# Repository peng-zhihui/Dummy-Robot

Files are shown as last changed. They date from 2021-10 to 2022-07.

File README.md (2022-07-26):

# Dummy-Robot: Super compact smart robotic-arm
> **我的超迷你机械臂机器人项目。**
>
> 视频介绍：[【自制】我造了一台 钢 铁 侠 的 机 械 臂 ！【硬核】](https://www.bilibili.com/video/BV12341117rG)
>
> Video : [I made a DUMMY ROBOTIC ARM from scratch！ - YouTube](https://www.youtube.com/watch?v=F29vrvUwqS4)

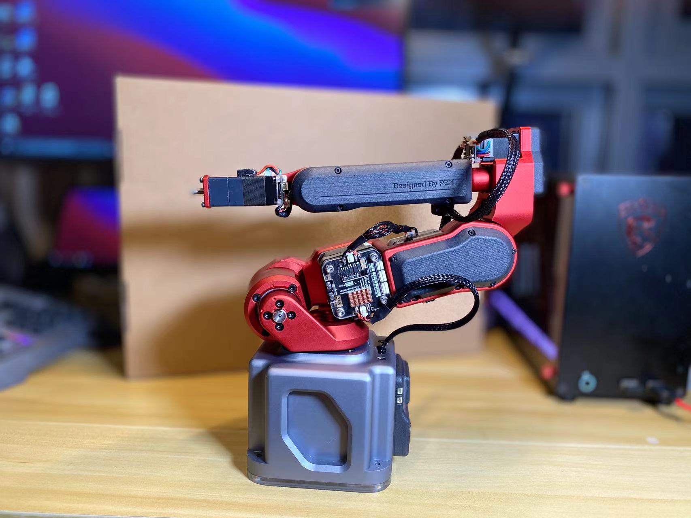
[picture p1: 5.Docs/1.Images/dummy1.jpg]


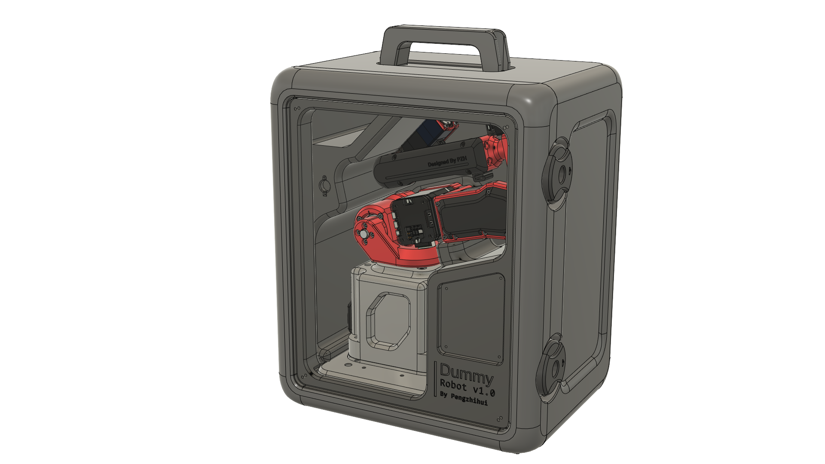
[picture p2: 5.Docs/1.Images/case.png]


### 资料说明（更新日期22-2-9）

* 已添加3D模型设计源文件。
* 已添加夹爪硬件设计文件和LED灯环PCB
* 已添加无线空间定位控制器PCB文件
* 已添加无线示教器Peak软硬件工程（作为submodule）
* 已添加REF的硬件设计文件
* 已添加DummyStudio上位机
* 已添加Dummy核心控制器的固件源代码（使用说明见后文）
* 已添加42步进电机驱动器硬件工程
* 已添加20步进电机驱动器硬件工程
* 已添加42/20步进电机驱动的固件源代码
* 已添加命令行调试工具reftool（基于odrivetool框架）
* 已添加便携手提箱的模型文件

> 这是视频中原版机械臂的完整设计方案，该方案成本和制作难度都比较高，因此想复现的同学建议再等等我后面会发布的**Dummy青春版**，该版本会有如下改进：
>
> 1. 整机重新设计结构，改用3D打印作为制造方案（原版为铝CNC），大幅降低制造成本
> 2. 采用我自己设计的小型摆线针轮减速器替代原版的谐波减速器，大幅降低零件成本
> 3. 所有软件和固件和原版通用，功能也完全一致
> 4. 添加我自己设计的PC端上位机和手机端APP（争取把用户初始化设置引导加进去）
> 5. 改进原版电机驱动器的走线方式，原版电源走线采用焊接的形式，不便于安装和拆卸，后面的青春版会使用4p接插件（电源+CAN总线）连接
> 6. 整机成本争取做到2000以内
> 7. **最重要的，会找人出一个保姆级的视频教程！**

## 关于结构设计

我视频中原版设计使用的`步进电机`+Harmonic的`谐波减速模组`，其中后者成本较高（我买的二手大概是600元一个），因此为了能让大家尽量复现本项目，我后期会添加一个`自制摆线针轮减速器`+`3D打印`的低成本方案。

> 目前摆线减速器已经设计好了正在验证，预期会使用PC（或者亚克力）切割结合3D打印制作，精度有所下降但是功能都保持不变，整机硬件成本希望控制在2000元以内。

设计好的摆线减速器见我的另一个仓库：[peng-zhihui/CycloidAcuratorNano ](https://github.com/peng-zhihui/CycloidAcuratorNano)

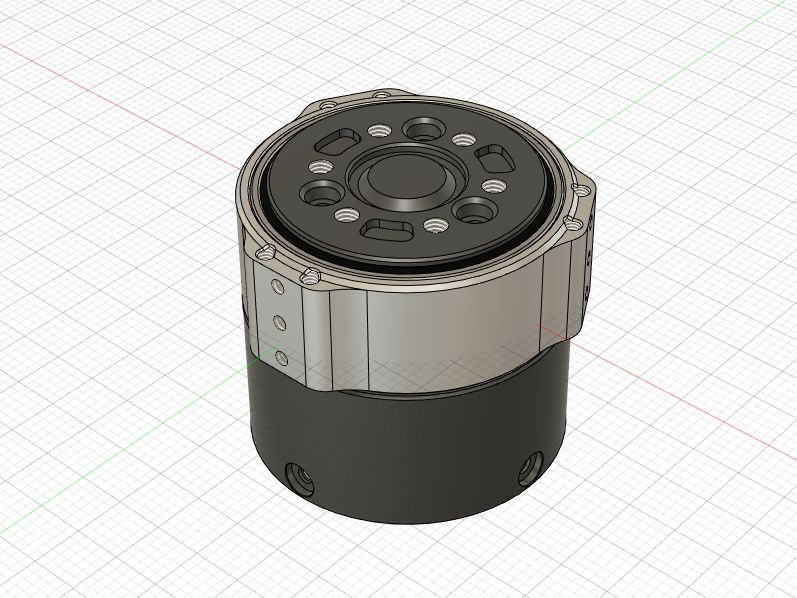
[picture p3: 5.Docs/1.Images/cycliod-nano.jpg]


## 关于电路模块

电路为了实现主要的机械臂运动控制功能其实核心就4块板子：

* REF核心板
* REF底板（也就是机械臂底座里面的控制器电路板）
* 步进电机驱动
* Peak示教器

其中前两者和Peak我都开源了，步进驱动设计的时候参考了： https://github.com/unlir/XDrive 这个项目，这是我一个朋友开源的闭环驱动，基于STM32。该驱动分为开源版和闭源版，闭源版基于分立MOSFET性能极其强劲且功能很完善，开源版用的ADC+斩波驱动芯片，具备基础功能，不带CAN协议。

我重新设计了驱动器的PCB电路（本项目分别用到20、42步进，57的文件只是供大家扩展使用），添加了CAN总线的硬件支持，也对原版核心代码进行了完全重构，**提供编译好的二进制文件可以直接烧录：**

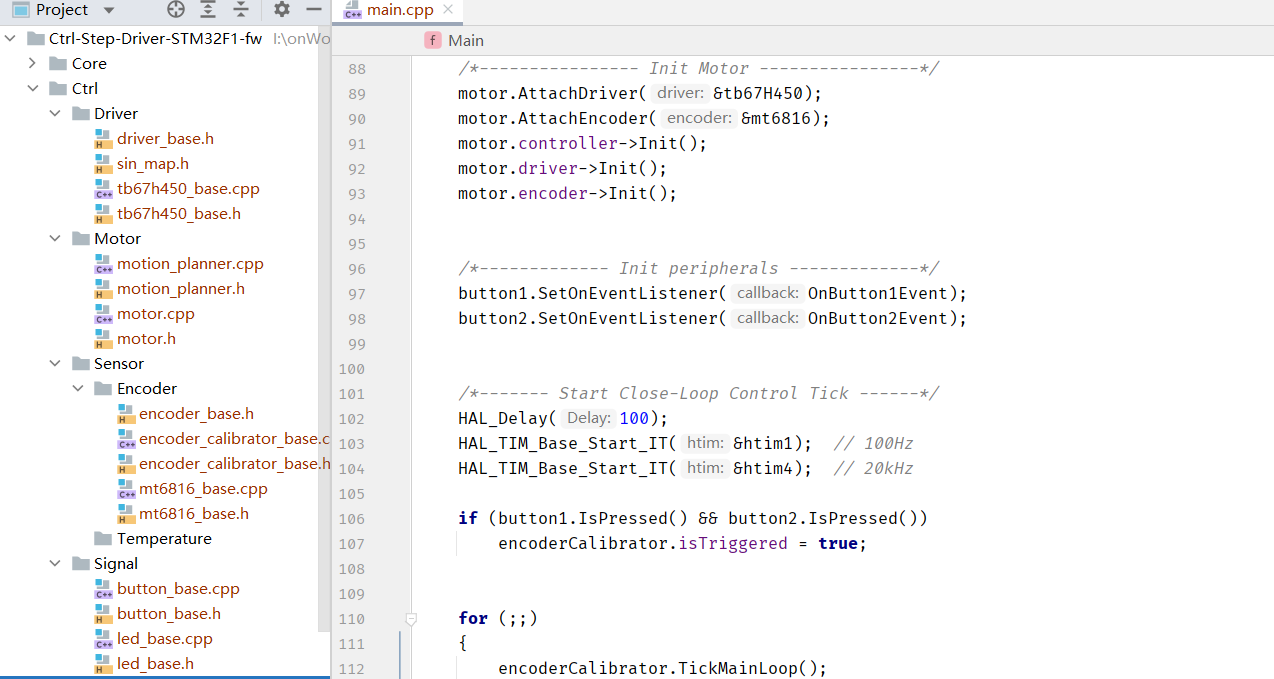
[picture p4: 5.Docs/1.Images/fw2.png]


**主要改进如下：**

1. 使用C++11重构了代码，引入很多高级语言特性，同时底层部分用C混编，不影响代码性能
2. 对硬件依赖完全解耦了，可以方便以后移植到其他平台的MCU，去除了冗余代码代码也结构化逻辑更加清晰
3. 添加了CAN协议和UART协议的自定义模板
4. 添加了模拟EEPROM的参数储存，可以断电保存数据
5. 添加了任意位置设置为零点，且保证双向半圈内归零（而不是单向归零）
6. 完全兼容STM32-HAL库，可以使用STM32CubeMX直接生成配置代码
7. 其他改进，大家二次开发仅需关注UserApp文件夹下的文件即可

Ctrl-Step驱动的使用方式比较简单，下载好固件后，第一次上电电机会进行编码器校准，如果成功则下次上电后按下按键1会进入闭环模式，通过CAN或者串口发送指令即可控制电机，关于指令的说明见源代码`UserApp`文件夹的`interface_can.cpp`和`interface_uart.cpp`：

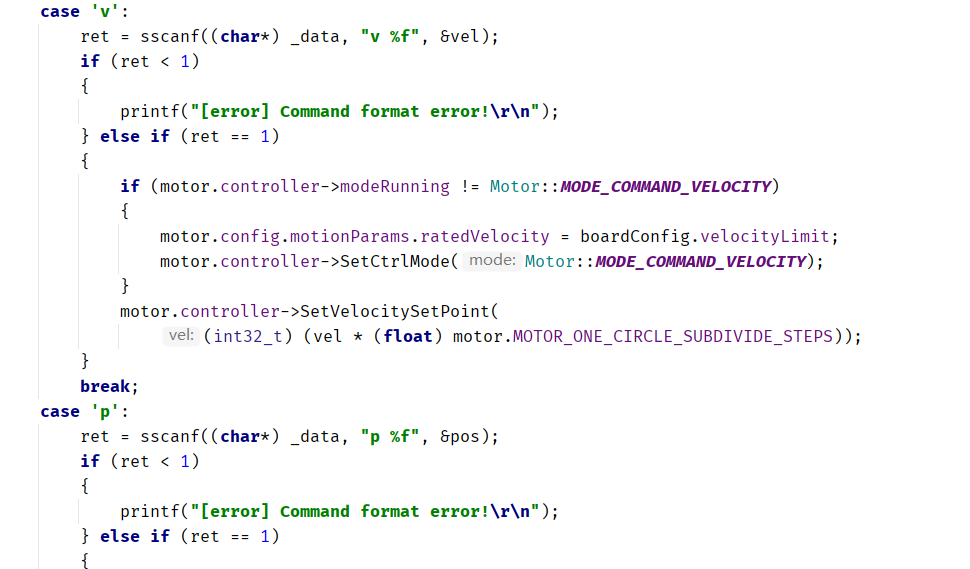
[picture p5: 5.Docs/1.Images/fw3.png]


> 其他按键的作用：
>
> * 同时按住两个按键上电，会自动进行编码器校准，如果首次校准失败可以通过这个方式重新校准
> * 短按按键1在**使能闭环/失能闭环**间切换
> * 长按按键1板子重启
> * 短按按键2清除堵转保护
> * 长按按键2将目标值归零（比如如果是在位置模式那位置会归零）
>
> 其他的功能要通过代码或者通信协议设置，比如设置**home零点**、**PID参数**、CAN节点ID、**各种运动参数**等等，可以自己研究代码。

当然另一种方式是大家也可以自行使用GRBL类的驱动器改装用来驱动本机械臂，这样方案的问题在于，grbl固件耦合性比较强（毕竟不是针对机械臂而是CNC类应用设计的）不便于扩展，另外脉冲形式的控制方式使得走线极其不优雅（每一个关节都要单独拉`step/dir`线到控制器，导致最后几个关节走线很长）。

而我用一体闭环的方式则可以以串联的形式把所有电机连起来即可，走CAN总线使得整体走线只需要四根线（电源正负两根，CAN信号线两根），此外总线模型使得电机可以工作在`力矩`、`速度`、`位置`、`轨迹`模式下，而脉冲模式只能工作在位置和轨迹模式，无法进行复杂控制。

**Peak的话我之前已经软硬件都开源了，可以去SubModules文件夹里面看那边的README说明。**

## 关于核心固件

这个机械臂的固件核心就是运动学姿态解算，~~这块我还在整理，后面会封装得更完善一些进行开源~~，**已开源**，现在写死的很多参数会设计成可配置的，**方便大家用本项目学习完后迁移到自己设计的机械臂中**；同时我把固件从LiteOS框架移植到大家更熟悉的FreeRTOS，方便做二次开发。

**REF的固件使用说明：**

固件主要包括几大功能模块：

* BSP驱动：板载的各种硬件驱动比如OLED、IMU、LED、蜂鸣器、非易失储存等等
* 3rdParty库：包括U8G2的图形库和Fibre的序列化/反序列化库
* Core：ST官方的HAL库
* Driver：ARM的CMSIS驱动
* Midwares：FreeRTOS支持包
* Robot：核心机器人库，包括各种算法和驱动代码
* UserApp：上层应用，可以基于我提供的API接口自行开发其他应用

> * 其中OLED使用Arduino的U8G2库移植而来，可以方便地现实各种调试和系统信息，另外由于STM32的硬件I2C又BUG这里使用了软件I2C驱动屏幕，实测帧率比硬件I2C更高。

`DummyRobot`类是Dummy的完整定义所在，初始化的时候需要设置好**步进电机驱动的信息**以及**自身的DH参数**：

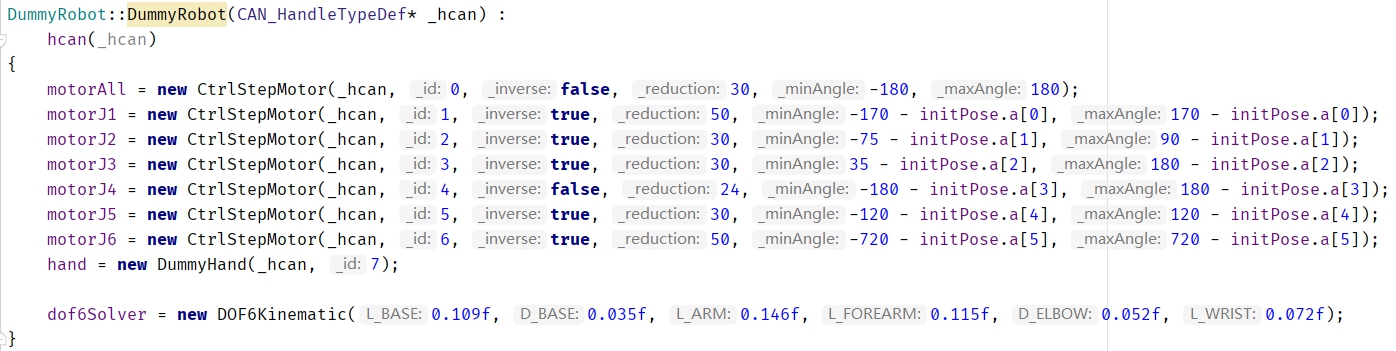
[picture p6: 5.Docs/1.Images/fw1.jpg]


其中驱动器信息包含：CAN节点ID、**是否反向**、减速器的减速比、**运动限制范围**。

而DH参数的含义如下：

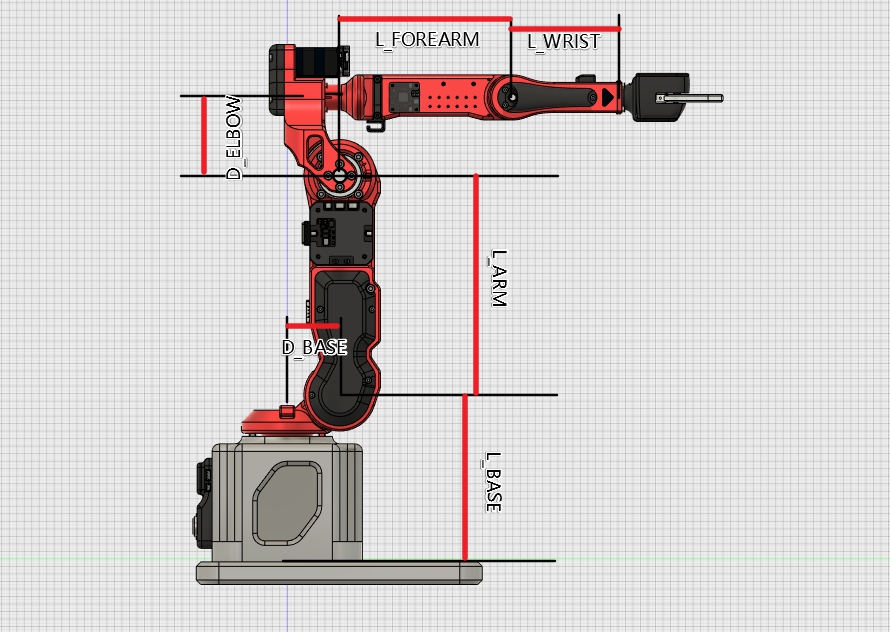
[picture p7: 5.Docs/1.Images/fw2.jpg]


机械臂的构型需要满足Pieper判据（机器人的三个相邻关节轴交于一点或三轴线平行），才能得出解析解，所以大家可以根据Dummy的结构进行修改，然后自己替换DH参数即可以移植我的代码。

> 关于位置的记忆，和上电零点校准：
>
> **由于绝对值编码器的位置只在一圈内有效，工业机械臂经过减速后为了获取绝对位置一般是做输出端编码，但是这样精度就降低了30倍（减速比），所以更合理的是做`双编码器`或者低`功耗编码器+电池`；而我这个项目中双编码器影响结构紧凑设计，所以用了更巧妙的方式：利用电机驱动的电流环控制上电后进行低力矩的无零点定向运动，碰到机械臂限位之后确认粗零点（无限位开关归零），然后根据单圈绝对值编码器的位置精调零点。这个方式的零点是没有误差的，而且几乎不受加工精度影响，因为在12度（360/30）内都是绝对值编码器的有效精度范围。**

**Peak的固件说明：**

Peak基于X-Track项目，大家可以去Peak仓库查看。

## 关于上位机

视频中的软件仿真基于RoboDK，我在视频中开发了连接Dummy的Driver（驱动部分官方document有介绍的，原版是基于TCP网络接口，我修改成了串口并兼容dummy的协议）。不过由于这个软件是收费的，因此我也基于Unity3D开发了自己的上位机，已经发布在仓库。

上位机目前暂时没有计划开源，因为还有很多功能要添加，我也是希望最后能做成一个类似RoboDK的通用软件，大家以后自己做机械臂也能用上，当然软件肯定会是免费的。

## 关于控制算法

首先运动学部分是已经实现了的，正逆解都是传统DH参数计算的，正解（关节角求末端位姿）是唯一解比较好办，逆解（末端位姿求关节角）的话会涉及多解（一般是8个），我这里使用的算法是**求解上一姿态和目标姿态中6个关节变化最大角里面最小的那一组作为逆解采用的config**。这样可以保证机械臂始终以最小转角进行姿态切换。

然后关节角到电机驱动器输入信号的转换这一块，我使用的是梯形加减速曲线进行速度位置规划。举个例子在MoveJ指令中，当收到一个关节角运动指令，控制器会进行运动角度差分计算，得到6个运动差分角度，然后取6个差分角中最大的角θ，同时根据设置的JointSpeed参数计算运动θ角需要的时间（考虑上加减速），把这一时间作为其余5个电机的运动参数计算各自的加减速度&最高速度，然后6个电机根据计算的参数同步运动，就可以保证其同步性和流畅性了。

另外六个电机使用CAN总线连接，每个电机接受两个ID号的信息（自己的ID、0号ID），0号ID作为信息广播和同步用。电机接收到运动指令后将信息储存在影子寄存器中，待收到广播的同步信号后开始运动，这样能进一步保证电机同步性。

最后，动力学部分还在开发中，这块暂时没有完全实现。上**述的运动学和动力学算法都强烈建议去看一下《机器人学导论》这本书**，里面写得非常详细。

## 指令模式

Dummy固件支持三种不同的指令模式（指令可以由USB、串口、CAN接收），不同模式的特性有所区别，见下表：

| | 指令发送频率 | 指令执行方式 | 可被新指令打断 | 指令间停顿 | 适合场景 |
| --- | --- | --- | --- | --- | --- |
| SEQ（顺序指令） | 随机，低（<5Hz）  | FIFO队列依次执行 | 否 | 有 | 一次性发送几个关键点位姿，等待依次执行，可以确保关键点到达；但是由于关键点之间存在减速到0的过程所以存在一定停顿；适合场景例如**视觉抓取、码垛等应用**。 |
| INT（实时指令） | 随机，频率不限 | 指令覆盖，立即执行 | 是 | 无 | 用于实时控制，新指令会覆盖正在执行的指令得到立即响应；但是如果一次性发送一系列指令的话则效果会是只执行最后一条；适合场景例如**动作同步**。 |
| `ToDo`TRJ（轨迹跟踪） | 固定，高（200Hz） | 自动插值，固定周期执行 | 否 | 无 | 适合用于需要进行精确轨迹跟踪的应用，速度会放慢；示例场景比如**3D打印、雕刻、绘画等**。 |

---

> **感谢以下项目作者：**
>
> * [unlir/XDrive: Stepper motor with multi-function interface and closed loop function. 具有多功能接口和闭环功能的步进电机。 (github.com)](https://github.com/unlir/XDrive)
> * [odriverobotics/ODrive: High performance motor control (github.com)](https://github.com/odriverobotics/ODrive)
> * [olikraus/u8g2: U8glib library for monochrome displays, version 2 (github.com)](https://github.com/olikraus/u8g2)
> * [samuelsadok/fibre: Abstraction layer for painlessly building object oriented distributed systems that just work (github.com)](https://github.com/samuelsadok/fibre)

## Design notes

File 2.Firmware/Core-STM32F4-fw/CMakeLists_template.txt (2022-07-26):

#THIS FILE IS AUTO GENERATED FROM THE TEMPLATE! DO NOT CHANGE!
set(CMAKE_SYSTEM_NAME Generic)
set(CMAKE_SYSTEM_VERSION 1)
cmake_minimum_required(VERSION 3.19)

# specify cross compilers and tools
set(CMAKE_C_COMPILER arm-none-eabi-gcc)
set(CMAKE_CXX_COMPILER arm-none-eabi-g++)
set(CMAKE_ASM_COMPILER arm-none-eabi-gcc)
set(CMAKE_AR arm-none-eabi-ar)
set(CMAKE_OBJCOPY arm-none-eabi-objcopy)
set(CMAKE_OBJDUMP arm-none-eabi-objdump)
set(SIZE arm-none-eabi-size)
set(CMAKE_TRY_COMPILE_TARGET_TYPE STATIC_LIBRARY)

# project settings
project(Core-STM32F4-fw C CXX ASM)
set(CMAKE_CXX_STANDARD 17)
set(CMAKE_C_STANDARD 11)

# for use printf & scanf with float
set(COMMON_FLAGS "-specs=nosys.specs -specs=nano.specs -u _printf_float -u _scanf_float")

#Uncomment for hardware floating point
add_compile_definitions(ARM_MATH_CM4;ARM_MATH_MATRIX_CHECK;ARM_MATH_ROUNDING)
add_compile_options(-mfloat-abi=hard -mfpu=fpv4-sp-d16)
add_link_options(-mfloat-abi=hard -mfpu=fpv4-sp-d16)

#Uncomment for software floating point
#add_compile_options(-mfloat-abi=soft)

add_compile_options(-mcpu=cortex-m4 -mthumb -mthumb-interwork)
add_compile_options(-ffunction-sections -fdata-sections -fno-common -fmessage-length=0)

# uncomment to mitigate c++17 absolute addresses warnings
#set(CMAKE_CXX_FLAGS "${CMAKE_CXX_FLAGS} -Wno-register")

if ("${CMAKE_BUILD_TYPE}" STREQUAL "Release")
    message(STATUS "Maximum optimization for speed")
    add_compile_options(-Ofast)
elseif ("${CMAKE_BUILD_TYPE}" STREQUAL "RelWithDebInfo")
    message(STATUS "Maximum optimization for speed, debug info included")
    add_compile_options(-Ofast -g)
elseif ("${CMAKE_BUILD_TYPE}" STREQUAL "MinSizeRel")
    message(STATUS "Maximum optimization for size")
    add_compile_options(-Os)
else ()
    message(STATUS "Minimal optimization, debug info included")
    add_compile_options(-Og -g)
endif ()

include_directories(
        Core/Inc
        Drivers/STM32F4xx_HAL_Driver/Inc
        Drivers/STM32F4xx_HAL_Driver/Inc/Legacy
        Drivers/CMSIS/Device/ST/STM32F4xx/Include
        Drivers/CMSIS/Include
        Middlewares/Third_Party/FreeRTOS/Source/include
        Middlewares/Third_Party/FreeRTOS/Source/CMSIS_RTOS_V2
        Middlewares/Third_Party/FreeRTOS/Source/portable/GCC/ARM_CM4F
        Middlewares/ST/STM32_USB_Device_Library/Core/Inc
        Middlewares/ST/STM32_USB_Device_Library/Class/CDC/Inc
        USB_DEVICE/App
        USB_DEVICE/Target
        3rdParty/fibre/cpp/include
        3rdParty/u8g2
        3rdParty/u8g2/cpp
        Bsp
        Bsp/imu
        Bsp/imu/filters
        Bsp/communication
        Bsp/memory
        Bsp/utils
        Bsp/gpio
        Bsp/utils/software_i2c
        Bsp/utils/arm_math
        Robot
        UserApp
)

add_definitions(-DUSE_HAL_DRIVER -DSTM32F4 -DSTM32F4xx -DSTM32F405xx -DconfigAPPLICATION_ALLOCATED_HEAP)

file(GLOB_RECURSE SOURCES
        "startup/*.*"
        "Drivers/*.*"
        "Core/*.*"
        "UserApp/*.*"
        "3rdParty/*.*"
        "Middlewares/*.*"
        "USB_DEVICE/*.*"
        "Robot/*.*"
        "Bsp/*.*"
        )

set(LINKER_SCRIPT ${CMAKE_SOURCE_DIR}/STM32F405RGTx_FLASH.ld)

add_link_options(-Wl,-gc-sections,--print-memory-usage,-Map=${PROJECT_BINARY_DIR}/${PROJECT_NAME}.map)
add_link_options(-mcpu=cortex-m4 -mthumb -mthumb-interwork)
add_link_options(-T ${LINKER_SCRIPT})

link_directories("Drivers/CMSIS/Lib")
link_libraries("arm_cortexM4lf_math.a")

add_executable(${PROJECT_NAME}.elf ${SOURCES} ${LINKER_SCRIPT})

set(HEX_FILE ${PROJECT_BINARY_DIR}/${PROJECT_NAME}.hex)
set(BIN_FILE ${PROJECT_BINARY_DIR}/${PROJECT_NAME}.bin)

add_custom_command(TARGET ${PROJECT_NAME}.elf POST_BUILD
        COMMAND ${CMAKE_OBJCOPY} -Oihex $<TARGET_FILE:${PROJECT_NAME}.elf> ${HEX_FILE}
        COMMAND ${CMAKE_OBJCOPY} -Obinary $<TARGET_FILE:${PROJECT_NAME}.elf> ${BIN_FILE}
        COMMENT "Building ${HEX_FILE}
Building ${BIN_FILE}")

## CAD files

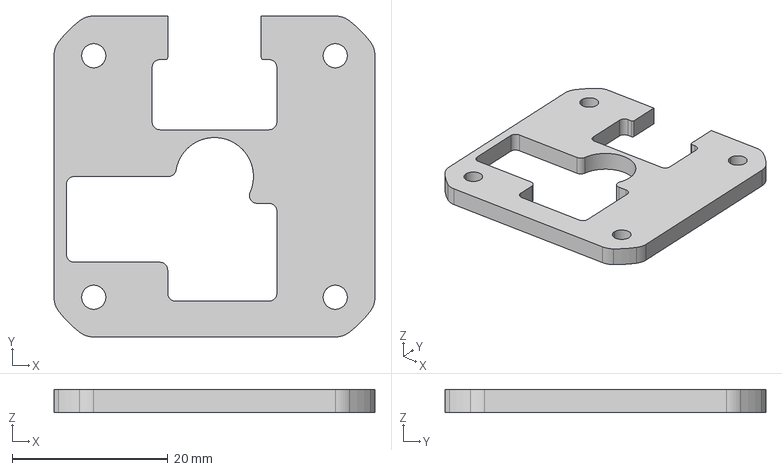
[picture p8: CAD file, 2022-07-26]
4.Model/Motor42-下盖.step
41.2 x 41.2 x 3.00 mm

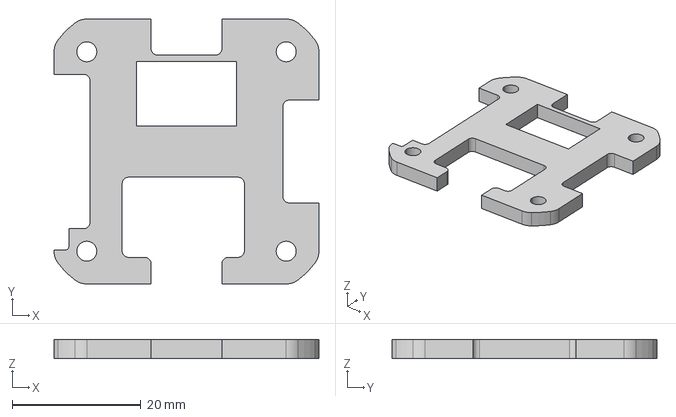
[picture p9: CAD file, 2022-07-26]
4.Model/Motor42-上盖.step
41.2 x 41.2 x 3.00 mm

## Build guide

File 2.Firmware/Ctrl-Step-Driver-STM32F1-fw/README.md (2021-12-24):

使用STM32CubeMX重新生成工程后，需要取消`stm32f1xx_it.c`的更改。

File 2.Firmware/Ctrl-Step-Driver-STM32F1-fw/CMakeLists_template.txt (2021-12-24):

#THIS FILE IS AUTO GENERATED FROM THE TEMPLATE! DO NOT CHANGE!
set(CMAKE_SYSTEM_NAME Generic)
set(CMAKE_SYSTEM_VERSION 1)
cmake_minimum_required(VERSION 3.20)

# specify cross compilers and tools
set(CMAKE_C_COMPILER arm-none-eabi-gcc)
set(CMAKE_CXX_COMPILER arm-none-eabi-g++)
set(CMAKE_ASM_COMPILER arm-none-eabi-gcc)
set(CMAKE_AR arm-none-eabi-ar)
set(CMAKE_OBJCOPY arm-none-eabi-objcopy)
set(CMAKE_OBJDUMP arm-none-eabi-objdump)
set(SIZE arm-none-eabi-size)
set(CMAKE_TRY_COMPILE_TARGET_TYPE STATIC_LIBRARY)

# project settings
project(Ctrl-Step-STM32-fw C CXX ASM)
set(CMAKE_CXX_STANDARD 17)
set(CMAKE_C_STANDARD 11)

#Uncomment for hardware floating point
#add_compile_definitions(ARM_MATH_CM4;ARM_MATH_MATRIX_CHECK;ARM_MATH_ROUNDING)
#add_compile_options(-mfloat-abi=hard -mfpu=fpv4-sp-d16)
#add_link_options(-mfloat-abi=hard -mfpu=fpv4-sp-d16)

#Uncomment for software floating point
#add_compile_options(-mfloat-abi=soft)

add_compile_options(-mcpu=cortex-m3 -mthumb -mthumb-interwork)
add_compile_options(-ffunction-sections -fdata-sections -fno-common -fmessage-length=0)

# uncomment to mitigate c++17 absolute addresses warnings
#set(CMAKE_CXX_FLAGS "${CMAKE_CXX_FLAGS} -Wno-register")

if ("${CMAKE_BUILD_TYPE}" STREQUAL "Release")
    message(STATUS "Maximum optimization for speed")
    add_compile_options(-Ofast)
elseif ("${CMAKE_BUILD_TYPE}" STREQUAL "RelWithDebInfo")
    message(STATUS "Maximum optimization for speed, debug info included")
    add_compile_options(-Ofast -g)
elseif ("${CMAKE_BUILD_TYPE}" STREQUAL "MinSizeRel")
    message(STATUS "Maximum optimization for size")
    add_compile_options(-Os)
else ()
    message(STATUS "Minimal optimization, debug info included")
    add_compile_options(-Og -g)
endif ()

include_directories(
        Core/Inc
        Drivers/STM32F1xx_HAL_Driver/Inc
        Drivers/STM32F1xx_HAL_Driver/Inc/Legacy
        Drivers/CMSIS/Device/ST/STM32F1xx/Include
        Drivers/CMSIS/Include
        Ctrl
        Ctrl/Sensor
        Ctrl/Signal
        Ctrl/LowLevel
        Ctrl/MotorControl
        UserApp
        Port
)

add_definitions(-DUSE_HAL_DRIVER -D__MICROLIB -DSTM32F1 -DSTM32F1xx -DSTM32F103xB)

file(GLOB_RECURSE SOURCES
        "startup/*.*"
        "Drivers/*.*"
        "Core/*.*"
        "Ctrl/*.*"
        "UserApp/*.*"
        "Port/*.*"
        )

set(LINKER_SCRIPT ${CMAKE_SOURCE_DIR}/STM32F103CBTx_FLASH.ld)

add_link_options(-Wl,-gc-sections,--print-memory-usage,-Map=${PROJECT_BINARY_DIR}/${PROJECT_NAME}.map)
add_link_options(-mcpu=cortex-m3 -mthumb -mthumb-interwork)
add_link_options(-T ${LINKER_SCRIPT})

add_executable(${PROJECT_NAME}.elf ${SOURCES} ${LINKER_SCRIPT})

set(HEX_FILE ${PROJECT_BINARY_DIR}/${PROJECT_NAME}.hex)
set(BIN_FILE ${PROJECT_BINARY_DIR}/${PROJECT_NAME}.bin)

add_custom_command(TARGET ${PROJECT_NAME}.elf POST_BUILD
        COMMAND ${CMAKE_OBJCOPY} -Oihex $<TARGET_FILE:${PROJECT_NAME}.elf> ${HEX_FILE}
        COMMAND ${CMAKE_OBJCOPY} -Obinary $<TARGET_FILE:${PROJECT_NAME}.elf> ${BIN_FILE}
        COMMENT "Building ${HEX_FILE}
Building ${BIN_FILE}")

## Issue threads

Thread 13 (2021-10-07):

求双目跟踪定位部分

xuebuaa, 2021-10-07:
红外LED辅助识别是提升定位精度吗？

APeiZou, 2021-10-08:
@peng-zhihui 双目跟踪定位用的什么算法啊

eqio, 2021-10-10:
@peng-zhihui 大神后面有什么简单的活，可以丢给我们练练手^_^。

peng-zhihui, 2021-10-19:
> @peng-zhihui 您好，这个[https://www.zhihu.com/question/36255080/answer/707967657项目的算法有开源吗？](https://www.zhihu.com/question/36255080/answer/707967657%E9%A1%B9%E7%9B%AE%E7%9A%84%E7%AE%97%E6%B3%95%E6%9C%89%E5%BC%80%E6%BA%90%E5%90%97%EF%BC%9F)

这个没有开源，很早以前在学校做的，我这边资料也不全了

fatsheep2020, 2024-02-18:
> 跟我的这个项目用到的技术是一样的： https://www.zhihu.com/question/36255080/answer/707967657
>
> 简单说就是，红外LED的图像经过二值化、轮廓查找得到大概位置，然后形态学处理和卡尔曼滤波得到精确预估位置，再用两个图像中的坐标视差计算Z轴深度得到三维坐标

这个链接不能访问了。。。

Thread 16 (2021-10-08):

请问工业设计 用什么软件，求技术路线，我也想自己学习做一套

weilingwei, 2021-10-08:
请问工业设计 用什么软件，求技术路线，我也想自己学习做一套

LeesCode, 2021-10-08:
法律问题我确实没想到（主要是免费的确实习以为常了，但严格来讲确实有风险）。不过就软件上手容易程度和后续静力动力仿真Solidworks更好一些，萝卜白菜各有所爱，还是看个人习惯。

eqio, 2021-10-08:
> 法律问题我确实没想到（主要是免费的确实习以为常了，但严格来讲确实有风险）。不过就软件上手容易程度和后续静力动力仿真Solidworks更好一些，萝卜白菜各有所爱，还是看个人习惯。

事实上，作者的开源已经算比较彻底了。虽然是通用格式，但大家都可以打开，如果想仔细研究，部分零件可以自己用自己习惯的软件重绘一次，也算加深印象了。

peng-zhihui, 2021-10-10:
我最开始用的Rhinoceros，去年转的Fusion360，f3d的文件别的软件打不开，step是最通用的，而且可以转成各种软件里的格式。

Q-fei, 2021-10-21:
fusion 360 感觉用起来不是很顺手，之前有用过，装配而言有点迷 反正我经常在装配的时候发生模型重叠现象 也不知道是不是我方法用错了，工业模型我用的还是soildworks

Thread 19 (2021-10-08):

同步现实部分能不能加在真正的中小型机械臂上阿

ZXin0305, 2021-10-08:
如题，如果可以的话，希望这一部分能够开源，也能够作为比较好的人机交互方式了，大神太强了！！！！

ballballu, 2021-10-08:
htc 有一个vive tracker。你可以用这个设备和这边的开源代码[vive-tracker](https://github.com/moon-wreckers/vive_tracker)，实现在ros框架下对机械臂的操作。我自己这边是用这个来遥操作ur5、tiago这样的机器人

ZXin0305, 2021-10-09:
> htc 有一个vive tracker。你可以用这个设备和这边的开源代码[vive-tracker](https://github.com/moon-wreckers/vive_tracker)，实现在ros框架下对机械臂的操作。我自己这边是用这个来遥操作ur5、tia

ZXin0305, 2021-10-09:
> htc 有一个vive tracker。你可以用这个设备和这边的开源代码[vive-tracker](https://github.com/moon-wreckers/vive_tracker)，实现在ros框架下对机械臂的操作。我自己这边是用这个来遥操作ur5、tiago这样的机器人

多谢，有时间去试一试

Closed 2021-10-09.

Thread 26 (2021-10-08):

有兴趣开源ps5力反馈扳机的相关代码么

ballballu, 2021-10-08:
今年2月做手持力反馈装置的时候考虑过ps5那个扳机，结果不是很理想。今年看了大佬做的这个，感觉好像很不错

peng-zhihui, 2021-10-10:
PS5手柄的扳机改造是把零件上的所有硬件连接到自己的PCB上控制反馈，相当于换主控，具体可以参考我发的原理图PCB

peng-zhihui, 2021-10-10:
代码开发时间原因其实实现得还很简单，就是几个PID控制环，这种反馈的效果主要受限于硬件，所以用PS5的硬件做效果可以很好

Closed 2021-10-10.

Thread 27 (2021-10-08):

有想要复现的同学一起拼个团吗？

Khala-Yang, 2021-10-08:
CNC金属外壳部分，不知道3D打印的可不可以 >_<

S1aoXuan, 2021-10-09:
准备跟组里的兄弟的复现但是硬件是着实不会>.<

Hconk, 2021-10-09:
建了个群有兴趣复现的可以一起讨论下(纯技术交流及成果分享),  希望可以使用其他的减速电机作为替代品，在尽量降低成本的同时能获得相对较高的精度， 一些物料如果批量做报价应该可以低些。 538103629

captain-zhang, 2021-10-09:
准备复现或者自制的同学可以加我啊，各方面都懂一点，可以团一个出来。QQ 741243893

Khala-Yang, 2021-10-09:
这么贵的吗！... 实属无知者无畏(捂脸)

billhhh, 2021-10-10:
举手，一起啊

xiangxing98, 2021-10-10:
赞一个

Khala-Yang, 2021-10-10:
逛了一圈GIthu，发现了有个便宜一点的 [SmallRobotArm](https://github.com/SkyentificGit/SmallRobotArm)，都是3D打印件，也没有用很贵的电机，预估千元以内，吃吃土还是拿的下的。
稚晖君的这个机械臂Sooo Sexy！但要复刻一个就真得喝西北风了...
我永远相信稚晖君的审美，可我的钱包不相信我>_<！

chenwh14, 2021-10-10:
初步看了一下模型，发现有CSF-8-30，CSF-5-30两种Harmonic的谐波减速器，全新的话不会便宜……二手的话应该也难有靠谱的渠道啊

Hconk, 2021-10-10:
> 初步看了一下模型，发现有CSF-8-30，CSF-5-30两种Harmonic的谐波减速器，全新的话不会便宜……二手的话应该也难有靠谱的渠道啊

从模型里面数了下用的电机。

电机 | 个数
-- | --
PK513PA-H50S | 3
CSF-5-30-1U | 2
CSF-8-30-1U | 2
Nema17 Stepper Motor | 2
CRK543AP-H50 | 1

peng-zhihui, 2021-10-10:
谐波的成本很高，其实我是希望有同学有空修改一下模型改成行星减速方案（其实也不难），然后3D打印机身，精度虽说和我视频中比不了，但是比一般的舵机机械臂是要强很多的，而且后面代码可以通用

SinKy-Yan, 2021-10-10:
其实行星的话感觉可以试试DJI的那两个给比赛做的电机，[M3508](https://www.robomaster.com/zh-CN/products/components/general/M3508)和[M2006](https://www.robomaster.com/zh-CN/products/components/general/M2006) 这两个的回差应该在可接受的范围内，不知道有没有大佬去看看

GitHubHun, 2021-10-11:
我来看看大家在聊什么我看不懂的东西;

Fanjustfan, 2021-10-12:
想要复现+1 大佬们有群吗 交流比较方便

liubog2008, 2021-10-13:
https://join.slack.com/t/just-for-funco/shared_invite/zt-wysbftd3-iguJ4uYk2n9TgtX6fmkx0A 发个 slack 链接，欢迎大家加入

willshion, 2021-10-13:
求行星 复现 1k左右踢我

captain-zhang, 2021-10-15:
> 求行星 复现 1k左右踢我

1K 你还是歇着吧

MuNineyi, 2021-12-14:
> https://join.slack.com/t/just-for-funco/shared_invite/zt-wysbftd3-iguJ4uYk2n9TgtX6fmkx0A 发个 slack 链接，欢迎大家加入

可以给个 slack 的邀请链接么，原连接过期了

fumingxi, 2021-12-20:
我3D打印了一套对应的金属件，强度还可以，不过对PCB之类的不通（纯软件出身）。。有没有大佬篇硬件的一起搞一下。？

StarJi1991, 2022-02-21:
查了一下这个电机价格是认真的？

52chengcheng, 2022-06-28:
有没有群，邀一下

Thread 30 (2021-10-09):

给大佬提个进一步开发建议。供参考。（另：第一次离大佬这么近！激动！！）

sipgov, 2021-10-09:
大佬可以考虑开发各种模块化的合成设备，比如机械臂+AI模块+智能自行系统，则可以化身成为战场上的智能医疗机器人。机械臂+矢量杠杠动力放大模块，就可以成为真正的工业生产机器人。这样将来商业化运作时，客户可以根据自己需求按需购买不同模块组合。

peng-zhihui, 2021-10-10:
我这些都是自己业余DIY项目所以没太考虑商业化哦，不过你说的模块化思路其实我是会做的

TANG-N, 2021-10-14:
有了这只手，加只眼，是不是就能陪打乒乓球了

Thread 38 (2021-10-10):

咨询zhihui兄，从事这些DIY平时的资金投入情况

jpixy, 2021-10-10:
很久之前，几乎是从zhihui君在大学时候作寻线机器人开始，就一直关注zhihui兄的DIY，也深受启发。

我最大的问题是，其实zhihui兄之前也曾透露过花过不少钱，但是一直没有一个具体的数量级。

所以，还是希望zhihui兄能否大概给出个从入门到平时开发的大体的资金投入，个人想得以参考：

1. 原材料的费用，小的电子元器件估计费用不大，但是一些CPU等重要芯片和制作PCB板子，和作废板子等费用应该投入不小(每次小几百，小一千，累积多了也不少费用估计)，能否具体说说？
2. 这个机械臂成品费用一万元左右，但是从开发到设计，debug，作废等考虑进去，总计会投入多少？
3. 由此，针对一般的DIY的开发，资金投入分布大概什么样子呢？比如作废板子大概占6,7成总费用等。能否给出个资金占比？当然详单更好。
4. 除了这些，那些工具一次性的投入，估计还好。不管是焊台，还是3D打印机基本上都是一次性投入，这部分也能出个大概的清单吗？
5. 总而言之，想知道zhihui兄，平时维持这个DIY爱好，资金投入的大体情况，以供参考。

不知道这个是不是敏感话题，之前在给您的个人邮箱pengzhihui.david@foxmail.com 发过邮件咨询类似问题。如果不方便在issue里公开回答，是否可以邮件给我: johnny@jpixy.com一些指导和答复？

谢谢！
Johnny

peng-zhihui, 2021-10-10:
1. 元器件库是持续积累的，比如可以去买一个电阻电容本，型号很全性价比也很高，除了最近出现的芯片涨上天的情况，其余器件有个1、2000元足够囤一堆了
2. 费用主要就是减速器和PCB打样，详细的没算，总之不超过2w吧
3. 上面说了，可以屯一个元件库，根据项目持续补充
4. 我以前报道里说过，我在大学为了买工具和元件做比赛，连饭都吃不起了，而我生活费也才一个月1000当时也做出了很多有意思的东西；所以投入这种事情往上了看就不封顶了，我条件好了之后买工具都是很舍得投入的，但是往下看，只要每月有个几百块也完全足够。

Closed 2021-10-10.

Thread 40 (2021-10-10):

关于位置的记忆，每次上电都需要零点校准吗？

eqio, 2021-10-10:
我的理解是步进的绝对位置是从上电开始计算的。在断电后是否需要归零，6个轴是分别校准的吗？

peng-zhihui, 2021-10-11:
绝对位置只在一圈内有效，经过减速后为了获取绝对位置一般是做输出端编码，但是这样精度就降低了30倍（减速比），所以更合理的是做双编码器，而我这个项目中双编码器影响结构紧凑设计，所以用了更巧妙的方式：利用电机驱动的电流环控制上电后进行低力矩的无零点定向运动，碰到机械臂限位之后确认零点。这个方式的零点是没有误差的，而且几乎不受加工精度影响，因为在12度（360/30）内都是绝对值编码器的有效精度范围。

eqio, 2021-10-11:
@peng-zhihui 小系统而言，您的实现已经很巧妙了。只是实际应用中限位开关好像也是必须的，且不一定每次能去零点校准，也许有工件。商业应用是另一个范畴，个人觉得。

zhbi98, 2025-05-23:
为什么 Dummy 要设置两次零点？第一次是 L 形的时候设置一下，复位姿势后在设置一下。在机械臂回到休息姿势（Resting Pose）后再应用一次“当前位置作为零点”（ApplyPositionAsHome），那么最后零点不就会以休息姿势来定义

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

Closed 2021-10-11.

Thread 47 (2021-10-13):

稚辉君你好，请问robodk部分的驱动会开源出来吗？

JunJie-zhang-o, 2021-10-13:

JunJie-zhang-o, 2021-10-13:
因为之前有修改过部分的离线编程的代码，但是关于驱动部分并没有做太多了解，看您视频中使用的是robodk的驱动，想学习下robodk驱动部分！！！

peng-zhihui, 2021-10-13:
驱动部分官方document有介绍的，原版是基于TCP网络接口，我修改成了串口，另外我自己的上位机已经更新了。

wxfzy, 2021-10-16:
稚晖君，你的上位机会开源吗？

yijiehe-oss, 2021-11-03:
在你的基础上在开发做创新可以吗？

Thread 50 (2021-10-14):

大佬，步进电机驱动好像没有放到文件里

Jzacky, 2021-10-14:

CaoZengxu, 2021-10-14:
大佬已经明确说了这部分不开源。建议写到readme里，防止大🔥还有不必要的期待。

Jzacky, 2021-10-14:
> > 大佬已经明确说了这部分不开源。建议写到readme里，防止大🔥还有不必要的期待。
>
> 没有说这部分不开源啊，是说会出一个简化版的开源。

哦哦，谢谢大佬

Riva34, 2021-10-30:
对呀，连我这个65岁的老骨头都在泰国慢慢学习。所有部件都要用两个星期时间寄到泰国。

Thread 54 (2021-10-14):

偶像能不能把上位机软件的项目代码也开源呀，想要学习学习

nishiwodelian, 2021-10-14:
感谢

HackEFA, 2021-10-14:
[Assembly-CSharp.zip](https://github.com/peng-zhihui/Dummy-Robot/files/7345792/Assembly-CSharp.zip)
SW: dnSpy
需要增加unity引擎引用

nishiwodelian, 2021-10-14:
> [Assembly-CSharp.zip](https://github.com/peng-zhihui/Dummy-Robot/files/7345792/Assembly-CSharp.zip) SW: dnSpy 需要增加unity引擎引用
太感谢了，除了这些脚本文件，完整的unity项目文件您还有吗

HackEFA, 2021-10-14:
那个你download下来dll就行，unity3D软件向导配置就可以加载需要的那部分插件，主要内容在这个C#里面。
可以参考https://www.youtube.com/watch?v=MQKJfZCAEa8
我并没有这个项目的全部工程，要看大佬是否开源了，C#这部分是主要机械臂实现的主要部分和接口。

nishiwodelian ***@***.***> 于2021年10月14日周四 下午8:37写道：

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

Ice-Panda, 2021-10-19:
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

稚晖君你好，我想请教一下Dummy Studio中，网格地板和右上角的坐标轴是如何实现的，为什么可以和编辑模式下几乎一样。

Closed 2021-10-14.

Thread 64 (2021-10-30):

代码注释 全英文的啊？

sampletea, 2021-10-30:

peng-zhihui, 2021-10-30:
是啊，因为很多外国友人也要做

peng-zhihui, 2021-10-30:
是啊，我注释一般习惯写英文，因为中文编码容易出问题，而且很多外国友人也要做

Alansortorz, 2021-10-30:
哈哈  太真实了  CLion哪个写32的程序，中文注释，动不动就成乱码了

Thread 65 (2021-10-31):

实际控制的入口是在哪 我看了这几个线程  就直接dummy.UpdateJointPos(); 里边用can发数据了？

sampletea, 2021-10-31:
CommunicationTask    ThreadOledUpdate   ThreadControlLoop  ？ 实际控制 目标位置 啊    计算姿态啥的 从哪里进去？
  对RTOS不是很懂 ！！！ 勉强看看这三个线程    大佬 指点一下！

peng-zhihui, 2021-11-04:
机械臂是接受上位机指令的，指令解析看protocol里面的代码，最终都是调用MoveJ和MoveL进行姿态解算

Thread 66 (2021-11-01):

咨询一下atlas200的开发套件相关的硬件配置。

wangweiqing, 2021-11-01:
hello，看到动作捕获那部分，使用了双目摄像头加一个atlas200的卡，想咨询一下，那个搭载atlas卡的开发板相关配置是什么？目前有有一些兴趣去做一下这部分相关的东西。

peng-zhihui, 2021-11-04:
https://e.huawei.com/cn/products/cloud-computing-dc/atlas/atlas-200
不过现在已经没有对外提供了，新一代产品明年会出

wangweiqing, 2021-11-04:
淘宝上还有存量的产品~只不过主要是4G的版本，8G版本的会比较少。

Closed 2021-11-04.

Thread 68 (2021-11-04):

DH参数好像不对？是不是我搞错了？D_ELBOW不应该是连杆的长度a吗？为啥是d

guguobao, 2021-11-04:
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

peng-zhihui, 2021-11-04:
你搞错了，D是连杆偏移，L才是长度，注意我模型里面是有角度Offset的，3轴的角度旋转了90度

guguobao, 2021-11-04:
> 你搞错了，D是连杆偏移，L才是长度，注意我模型里面是有角度Offset的，3轴的角度旋转了90度
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
D_ELBOW连杆偏移好像是沿着关节3的Z轴偏移的是吧？
但我看实物D_ELBOW更像是连杆的长度，沿着关节3的x轴偏移。总觉得和实物不太符合？我用的是标准DH建模思路，不知道思路对不对？望大佬指点

guguobao, 2021-11-04:
我猜你的正解并没有使用到DH参数中的d和a，因此你的程序在使用中是没问题的，

guguobao, 2021-11-04:
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
想请教下L1_BASE、L2_ARM、L3_ELBOW、L6_WRIST这四个向量的初始值缘由？

peng-zhihui, 2021-11-04:
当然用了啊，不用怎么正逆解，代码里都有

发自我的iPhone

------------------ 原始邮件 ------------------
发件人: guguobao ***@***.***&gt;
发送时间: 2021年11月4日 13:54
收件人: peng-zhihui/Dummy-Robot ***@***.***&gt;
抄送: 稚晖 ***@***.***&gt;, Comment ***@***.***&gt;
主题: 回复：[peng-zhihui/Dummy-Robot] DH参数好像不对？是不是我搞错了？D_ELBOW不应该是连杆的长度a吗？为啥是d (Issue #68)

peng-zhihui, 2021-11-04:
你把机械臂三轴抬起90度机械臂竖直一条线就会明白了

发自我的iPhone

------------------ 原始邮件 ------------------
发件人: guguobao ***@***.***&gt;
发送时间: 2021年11月4日 13:54
收件人: peng-zhihui/Dummy-Robot ***@***.***&gt;
抄送: 稚晖 ***@***.***&gt;, Comment ***@***.***&gt;
主题: 回复：[peng-zhihui/Dummy-Robot] DH参数好像不对？是不是我搞错了？D_ELBOW不应该是连杆的长度a吗？为啥是d (Issue #68)

peng-zhihui, 2021-11-04:
> 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 想请教下L1_BASE、L2_ARM、L3_ELBOW、L6_WRIST这四个向量的初始值缘由？

坐标系是右手坐标，图中右为X+，上为Z+；那个d/a只是临时变量，没有用到，后面实际直接用DH_matrix里面的变量了

guguobao, 2021-11-04:
好的，我刚刚猜到了L1_BASE、L2_ARM、L3_ELBOW、L6_WRIST的定义的，是不是这样的，比如L1_BASE= {armConfig.D_BASE, -armConfig.L_BASE, 0.0f}，L1_BASE即是把D_BASE看成在R[0]旋转后的坐标系x轴方向的值,  L_BASE看成R[0]旋转后的坐标系y轴方向的值 ,
如图：

guguobao, 2021-11-04:
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

guguobao, 2021-11-04:
望指导，十分感谢

peng-zhihui, 2021-11-04:
> 望指导，十分感谢

是的理解正确，简单讲L都是本身臂长，D是和臂长垂直方向的偏移

peng-zhihui, 2021-11-04:
另外初始角度偏移90°是当时为了和RoboDK里面的参数匹配

guguobao, 2021-11-04:
好的，谢谢了，我还想问问逆解，有什么好的方法理解 关节2有四组解，每组解得几何推导，有点难理解

guguobao, 2021-11-04:
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

peng-zhihui, 2021-11-04:
可以看一下林沛群教授的视频课程，讲得很好

发自我的iPhone

------------------ 原始邮件 ------------------
发件人: guguobao ***@***.***&gt;
发送时间: 2021年11月4日 20:35
收件人: peng-zhihui/Dummy-Robot ***@***.***&gt;
抄送: 稚晖 ***@***.***&gt;, Comment ***@***.***&gt;
主题: 回复：[peng-zhihui/Dummy-Robot] DH参数好像不对？是不是我搞错了？D_ELBOW不应该是连杆的长度a吗？为啥是d (Issue #68)

好的，谢谢了，我还想问问逆解，有什么好的方法理解 关节2有四组解，每组解得几何推导，有点难理解

—
You are receiving this because you commented.
Reply to this email directly, view it on GitHub, or unsubscribe.
Triage notifications on the go with GitHub Mobile for iOS or Android.

guguobao, 2021-11-05:
我又来麻烦你了，林沛群得机器人学我看完逆解部分了，它仅仅提到欧拉角zyz，没有提到已知zyz欧拉矩阵去反推角度。zyz欧拉矩阵（好像就是等同rotz(theta4)*roty(theta5)*rotz(theta6)（右乘，相对旋转），正好对上关节4坐标z、关节5坐标系y、关节6坐标z），逆解前面代码我看懂了，求关节1（左右手）、关节2（正反手）和关节3（关节2确定，关节3也就确定了）我几何推出来了，现在看不懂R36矩阵是如何一步一步反推关节5、4、6，我参照《机器人学导论-原书第四版》得p34页，书上有明确得公式去反推计算欧拉角，但发现和代码中得不是很匹配，我想问下，是要深刻理解欧拉角旋转矩阵形成，不一定按书上公式也可以？但我不知如何理解它，如何理解你的atan2去代入R36矩阵得值一步一步去计算，书上得公式是怎么来的，书也没有说？好抽象，求指点或者书籍推荐，

msnh2012, 2021-11-05:
关于姿态学，可以看看我这个repo. https://github.com/msnh2012/Msnhnet/tree/master/src/math

sampletea, 2021-11-12:
基座坐标系 和 i1-i6坐标系分别建在哪里？  我画到i5就没找不着了

guguobao, 2021-11-12:
> 基座坐标系 和 i1-i6坐标系分别建在哪里？ 我画到i5就没找不着了

在关节6末端，最后一个连杆的末端，标准DH建模的坐标系在连杆的末端

sampletea, 2021-11-12:
> > 基座坐标系 和 i1-i6坐标系分别建在哪里？ 我画到i5就没找不着了
>
> 在关节6末端，最后一个连杆的末端，标准DH建模的坐标系在连杆的末端

大佬能 不能画一整个建好的图 出来 我看看我哪里错了

Gzlaughing, 2021-12-11:
> 我又来麻烦你了，林沛群得机器人学我看完逆解部分了，它仅仅提到欧拉角zyz，没有提到已知zyz欧拉矩阵去反推角度。zyz欧拉矩阵（好像就是等同rotz(theta4)*roty(theta5)*rotz(theta6)（右乘，相对旋转），正好对上关节4坐标z、关节5坐标系y、关节6坐标z），逆解前面代码我看懂了，求关节1（左右手）、关节2（正反手）和关节3（关节2确定，关节3也就确定了）我几何推出来了，现在看不懂R36矩阵是如何一步一步反推关节5、4、6，我参照《机器人学导论-原书第四版》得p34页，书上有明确得公式去反推计算欧拉角，但发现和代码中得不是很匹配，我想问下，是要深刻理解欧拉角旋转矩阵形成，不一定按书上公式也可以？但我不知如何理解它，如何理解你的atan2去代入R36矩阵得值一步一步去计算，书上得公式是怎么来的，书也没有说？好抽象，求指点或者书籍推荐，

就是矩阵运算，稚辉君的正逆解是用了3x3的矩阵，机器人学导论是4x4的。可以去看MIT公开课的线性代数，理解一下矩阵的几何含义。

a361251388, 2022-04-02:
> 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

这个问题解决了吗，我也推算D_ELBOW是a？ 沿z2方向看，x2和x3之间d为0；沿x3方向，z2和z3的距离为D_ELBOW，旋转90度打直也也不对呀

LZD0502, 2022-04-26:
您好 逆解法的代码您能解答下吗？

MatMultiply(R06, L6_WRIST, L0_wt, 3, 3, 1); 乘出来的L0_WRIST是啥意思，这一步没怎么懂。

MatMultiply(R10, P0_w, P1_w, 3, 3, 1);这个R10不就是A1的逆嘛，乘出来的P1_w又是啥

LZD0502, 2022-04-29:
> 可以看一下林沛群教授的视频课程，讲得很好 发自我的iPhone
> […](#)
> ------------------ 原始邮件 ------------------ 发件人: guguobao ***@***.***&gt; 发送时间: 2021年11月4日 20:35 收件人: peng-zhihui/Dummy-Robot ***@***.***&gt; 抄送: 稚晖 ***@***.***&gt;, Comment ***@***.***&gt; 主题: 回复：[peng-zhihui/Dummy-Robot] DH参数好像不对？是不是我搞错了？D_ELBOW不应该是连杆的长度a吗？为啥是d (Issue #68) 好的，谢谢了，我还想问问逆解，有什么好的方法理解 关节2有四组解，每组解得几何推导，有点难理解 — You are receiving this because you commented. Reply to this email directly, view it on GitHub, or unsubscribe. Triage notifications on the go with GitHub Mobile for iOS or Android.

您好 逆解法这部分代码 有没有详细点的解释啊

tongchuyan, 2022-07-27:
> > 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
>
> 这个问题解决了吗，我也推算D_ELBOW是a？ 沿z2方向看，x2和x3之间d为0；沿x3方向，z2和z3的距离为D_ELBOW，旋转90度打直也也不对呀

你好，问一下解决了吗？我也觉得应该是a

tongchuyan, 2022-07-27:
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

我也这么觉得，问一下解决了吗？

qq302011, 2022-09-20:
哪位大佬能否解释下这个第五个关节怎么l和d都是0呢？另外我通过software里面的仿真软件改变第六个关节的角度，没有发现任何变化？第六个关节在哪呢？

adsl7878778, 2023-01-05:
个人感觉是坐标系建立不同的问题，不过用大佬的DH参数进行仿真，确实会出现上述问题，看起来与实物不符，自己进行DH参数建立，和大佬的与一些不同之处，但在进行仿真的时候，各关节位置和实物是一致的，具体什么原因我也不是很清楚，可能体现在代码里？还没有看。
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
用大佬的参数仿真出来是这样的
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
用自己的DH参数仿真出来是这样的
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
也不知道哪个对，继续往下学习再说吧，如果能有大佬解释一下就最好了

hhjhz, 2023-08-07:
> 个人感觉是坐标系建立不同的问题，不过用大佬的DH参数进行仿真，确实会出现上述问题，看起来与实物不符，自己进行DH参数建立，和大佬的与一些不同之处，但在进行仿真的时候，各关节位置和实物是一致的，具体什么原因我也不是很清楚，可能体现在代码里？还没有看。 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 用大佬的参数仿真出来是这样的 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 用自己的DH参数仿真出来是这样的 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 也不知道哪个对，继续往下学习再说吧，如果能有大佬解释一下就最好了

我也是这样，请问问题解决了吗？

Closed 2021-11-14.

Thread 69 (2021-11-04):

稚晖君你好，请问双目相机部分用的什么算法？

ddg238, 2021-11-04:
在 #13 你之前提供的链接已经失效了，能否再提供一个双目这方面的详细思路呢，谢谢

zjw11111, 2021-11-08:
我也想了解一下这方面的东西，可以交流一下

peng-zhihui, 2021-11-17:
http://www.pengzhihui.xyz/2017/04/25/pingpong/

Gzlaughing, 2021-12-11:
哈哈哈哈，仿佛看到网上的那个段子，偷偷努力然后惊艳所有人。原来大佬17年就有想法要搞的，这下真的惊艳了所有人

fatsheep2020, 2024-02-18:
> http://www.pengzhihui.xyz/2017/04/25/pingpong/

这个链接不能访问了

CoderSuHang, 2024-02-18:
您好，我是苏航，感谢您的来信！我会尽快对来信进行查看并尽快给您进行回复，祝您身体健康，工作顺利，谢谢！

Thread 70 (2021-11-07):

关于步进电机驱动can通信问题

WSTRN, 2021-11-07:
请问步进电机驱动can通信的部分，软件框架是不是和odrive里的can类似呢？或者可以分享你的驱动固件源码来学习吗？ 感谢大佬指点

Whitolf, 2021-11-14:
通讯部分应该是和odrive 0.4.12的通讯一样，基于fibre的

Whitolf, 2021-11-14:
> 请问步进电机驱动can通信的部分，软件框架是不是和odrive里的can类似呢？或者可以分享你的驱动固件源码来学习吗？ 感谢大佬指点

通讯部分应该是和odrive 0.4.12的通讯一样，基于fibre的

WSTRN, 2021-11-16:
> > 请问步进电机驱动can通信的部分，软件框架是不是和odrive里的can类似呢？或者可以分享你的驱动固件源码来学习吗？ 感谢大佬指点
>
> 通讯部分应该是和odrive 0.4.12的通讯一样，基于fibre的

谢谢我去研究研究

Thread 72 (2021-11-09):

这里有 几个问题 梯形加减速规划 是写在步进驱动板里的啊? 好像CAN仅发了目标角度和 时间啊？

sampletea, 2021-11-09:
dummy.UpdateJointPos();  这里边是获取每个电机旋转了多少°吗？ float time = dummy.MoveJ(pose[0], pose[1], pose[2],
                                     pose[3], pose[4], pose[5]); 这  6个pose   是指每个电机 的目标角度 ？
 怎么 执行MoveL的 时候 需要 进行一边 逆解dof6Solver->SolveIK(pose6D, lastJoint6D, ikSolves);  之后在跟着MoveJ  ;;           MoveJ 不需要调用SolveFK() 的么？
 MoveJoints();    发送 目标角度 和 时间 到步进驱动器了啊  没看到梯形加减速规划呢  梯形加减速规划是写在 步进驱动板里的啊？

doche, 2021-11-13:
同问，没看到所说的梯形加减速，请指点，谢谢

peng-zhihui, 2021-11-17:
力矩、速度、位置、轨迹规划闭环都在驱动器里，因为我这里是总线控制，不是grbl那种脉冲同步控制，放在驱动器里才是合理的

sampletea, 2021-11-17:
> 力矩、速度、位置、轨迹规划闭环都在驱动器里，因为我这里是总线控制，不是grbl那种脉冲同步控制，放在驱动器里才是合理的

好的吧；  ！！   剩下的还能 解答一下吗？

vinsono, 2024-01-16:
SetPositionWithVelocityLimit(float _pos, float _vel)角度增量和最大速度到驱动，每个轴单独做插补和梯形加减速，没有做多轴联动的插补，所以无法实现直线和圆弧这种运动。

CoderSuHang, 2024-01-16:
您好，我是苏航，感谢您的来信！我会尽快对来信进行查看并尽快给您进行回复，祝您身体健康，工作顺利，谢谢！

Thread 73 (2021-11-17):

3D模型文件打不开，使用什么软件？

ouyangxin95, 2021-11-17:
Dummy v164.step这个文件我用SolidWorks2016打不开。请问你们是用的什么软件设计，CAD吗？

Colin-Ji, 2021-11-17:
.step文件应该是３维文件的通用交换格式，一般的三维软件应该都可以，你看下你的导入方式，不行的话用其他的软件试下

------------------&nbsp;原始邮件&nbsp;------------------
发件人:                                                                                                                        "peng-zhihui/Dummy-Robot"                                                                                    ***@***.***&gt;;
发送时间:&nbsp;2021年11月17日(星期三) 上午10:08
***@***.***&gt;;
***@***.***&gt;;
主题:&nbsp;[peng-zhihui/Dummy-Robot] 3D模型文件打不开，使用什么软件？ (Issue #73)

Dummy v164.step这个文件我用SolidWorks2016打不开。请问你们是用的什么软件设计，CAD吗？

—
You are receiving this because you are subscribed to this thread.
Reply to this email directly, view it on GitHub, or unsubscribe.
Triage notifications on the go with GitHub Mobile for iOS or Android.

echoeswang, 2021-11-18:
你随便 我用这个 Fusion 360

PancenHuang, 2021-11-19:
是不是你的SoildWorks软件版本比较旧，好像是比较旧的版本无法打开新版本画的图

AkrumIdrees, 2021-11-29:
I faced the same problem, the file is corrupt
I used SolidWorks and Fusion on multiple computers with no Luck!

PancenHuang, 2021-11-29:
> I faced the same problem, the file is corrupt I used SolidWorks and Fusion on multiple computers with no Luck!

My dear friend，Which version did you choose.My SoildWorks is 2020,Try changing the version？

AkrumIdrees, 2021-11-29:
> > I faced the same problem, the file is corrupt I used SolidWorks and Fusion on multiple computers with no Luck!
>
> My dear friend，Which version did you choose. My SoildWorks is 2020,Try changing the version？

I used SW 2017, SW2019 and Fusion latest Version. All Failed. I suggest uploading in Parasolid X_T., its is more stable than STEP.

PancenHuang, 2021-11-29:
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
You can try a different version，Maybe  he used SoildWorks 2020 to draw the Model.In Our life we usually export STEP for easy.

Philips-Luo, 2022-04-06:
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

My dear friend, I can read files normally with PROE5.0 without any problem.

chedy028, 2022-04-11:
I use sharp3d, can not open the file as well.

fumingxi, 2022-04-12:
Try Fusion 360.

chedy028, 2022-04-13:
>

Hey, Thanks. I tried, still not working

fumingxi, 2022-04-14:
Could you please attach the screenshot of error while opening?
I just downloaded the latest one and verified it was working.

Philips-Luo, 2022-04-14:
Dear friends,

[PENG-ZHIhui/dummy-Robot]: Dummyv164.step is designed using Fusion360 and exported as a. Step file. You can use other 3D model software and open it as an import. I use Pro/Engineer5.0 to open the file directly.

Philips-Luo, 2022-04-14:
Dear friends,

[PENG-ZHIhui/dummy-Robot]: Dummyv164.step is designed using Fusion360 and exported as a. Step file. You can use other 3D model software and open it as an import. I use Pro/Engineer5.0 to open the file directly.

------------------&nbsp;原始邮件&nbsp;------------------
发件人:                                                                                                                        "peng-zhihui/Dummy-Robot"                                                                                    ***@***.***&gt;;
发送时间:&nbsp;2022年4月14日(星期四) 上午8:31
***@***.***&gt;;
抄送:&nbsp;"ph ***@***.******@***.***&gt;;
主题:&nbsp;Re: [peng-zhihui/Dummy-Robot] 3D模型文件打不开，使用什么软件？ (Issue #73)

Could you please attach the screenshot of error while opening?
 I just downloaded the latest one and verified it was working.

—
Reply to this email directly, view it on GitHub, or unsubscribe.
You are receiving this because you commented.Message ID: ***@***.***&gt;

chedy028, 2022-04-14:
> Could you please attach the screenshot of error while opening?
>
> I just downloaded the latest one and verified it was working.

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

Philips-Luo, 2022-04-14:
chedy028:

&nbsp; &nbsp; &nbsp; &nbsp; &nbsp; Yes, but I can only take screenshots for you in my free time.

------------------ 原始邮件 ------------------
发件人:                                                                                                                        "peng-zhihui/Dummy-Robot"                                                                                    ***@***.***&gt;;
发送时间:&nbsp;2022年4月14日(星期四) 上午10:56
***@***.***&gt;;
抄送:&nbsp;"ph ***@***.******@***.***&gt;;
主题:&nbsp;Re: [peng-zhihui/Dummy-Robot] 3D模型文件打不开，使用什么软件？ (Issue #73)

Could you please attach the screenshot of error while opening?

I just downloaded the latest one and verified it was working.

—
Reply to this email directly, view it on GitHub, or unsubscribe.
You are receiving this because you commented.Message ID: ***@***.***&gt;

chedy028, 2022-04-14:
[](url)> Could you please attach the screenshot of error while opening? I just downloaded the latest one and verified it was working.
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
Another screenshot. The file was corrupted. don't know why, tried both on Mac and Ipad.

I probably should use Windows.

chedy028, 2022-04-14:
> > Could you please attach the screenshot of error while opening? I just downloaded the latest one and verified it was working. 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 Another screenshot. The file was corrupted. don't know why, tried both on Mac and Ipad.
>
> I probably should use Windows.

I fixed it !!!!!. simply git clone rather than download it directly from the github.

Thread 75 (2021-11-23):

电机驱动板PCB问题

cacazjj, 2021-11-23:
你好稚晖君，我用Altium Designer打开Motor PCB发现里面的板子和你在视频里的不太一样，比如视频里的pcb上有Signal，可是github里面的没有，是我打开方式不对么？麻烦你啦

peng-zhihui, 2021-11-27:
那些是脉冲驱动接口，在本项目里没用到我去掉了，用CAN总线控制。

cacazjj, 2021-11-28:
哦，太感谢啦。

BillCai06, 2022-05-23:
你好稚晖君, 我很喜欢你的设计，但是我在尝试制作电机驱动版的时候遇到不少麻烦。
一个是0402的原件本身就非常小了，而供电部分的原件密度又非常高，对于手残党的我来说实在是太挑战了。
还有就是因为芯片紧张的问题，导致我需要从多个网站购买元件，而很多国内的元器件这些国外网站（digi-kit, mouser)都没有。（人在国外，没有淘宝）比如MT6816 我需要从LCSC购买。 这导致了板子的成本直线上升（大概每块30多美金）。
如果大佬准备出青春版的驱动板，可以稍微降低一些元件的密集度吗，这样我这些人菜瘾大的手残党还有一丝丝机会复刻大佬作品。如果列出一些可以替换的等效IC就更好了。无论如何，感谢大佬分享自己的作品。

Andy-jg, 2025-01-24:
我可以把项目霍尔检测，更改成目前常规的霍尔芯片，比如 HAL 3900 MT6511 MLX90363

CoderSuHang, 2025-01-24:
您好，我是苏航，感谢您的来信！我会尽快对来信进行查看并尽快给您进行回复，祝您身体健康，工作顺利，谢谢！

Andy-jg, 2025-01-24:
同时，CAN 驱动的代码也要优化，调整为尝试重传，busoff 启用。

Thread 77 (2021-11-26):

无刷电机实现

Xi-MingYu, 2021-11-26:
步进电机换成无刷电机的方案有什么问题吗，看你之前做了foc的驱动板，为什么后来没有用无刷电机的方案

peng-zhihui, 2021-11-27:
步进电机能实现一样的效果（可以力矩、速度、位置控制），而且精度更高（极对数50对比无刷的十几），电机成本更低（几十块对比几百块），驱动器成本更低（自制的一体闭环成本几十对于无刷的成本200左右），更为什么不用步进电机呢？

peng-zhihui, 2021-11-27:
无刷的优势在于高转速下扭矩特性和整体功率密度大于步进，做大型机器人用无刷合适，做我这个项目用步进显然更好，不是无脑选择方案的。

Xi-MingYu, 2021-12-08:
明白了，最近也是想研究一下这个项目，感谢解惑

mailonghua, 2021-12-09:
请教一下，步进如何能像BLDC机械臂一样通过电流环路的控制进而对力进行控制，当前步进电机如何实现这样的效果？
多谢

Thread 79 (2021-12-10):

请教一下，步进如何能像BLDC机械臂一样通过电流环路的控制进而对力进行控制，当前步进电机如何实现这样的效果？

mailonghua, 2021-12-10:
请教一下，步进如何能像BLDC机械臂一样通过电流环路的控制进而对力进行控制，当前步进电机如何实现这样的效果？
多谢

_Originally posted by @mailonghua in https://github.com/peng-zhihui/Dummy-Robot/issues/77#issuecomment-989757449_

mailonghua, 2021-12-11:
是斩波驱动芯片来形成一个类电流环路吗？通过pwm/dac控制斩波驱动芯片的vref，然后采集反馈，是这样吗

gannerfreer, 2022-01-03:
我看着没有采集，应该是用芯片内部的闭环控制的电流

peng-zhihui, 2022-01-04:
斩波芯片进行电流控制，读一下驱动器源码

Closed 2022-03-15.

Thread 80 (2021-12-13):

Peak 和Dummy 是如何建立连接的

learner-f, 2021-12-13:
稚晖君你好，我在开启ref和peak后，屏幕上没有出现蓝牙标志，是我在peak或dummy中少了哪些操作或程序导致它们连不上吗，另外我看到你的视频中10：43左右，当时的peak是已经连上dummy了吗，似乎peak上显示的joints和pose3D的参数是默认的Homing数值，而机械臂的状态是Resting，这一点我不太明白希望能解惑，感谢

peng-zhihui, 2021-12-13:
需要自己修改代码设置配对的mac地址，建议完整读一下代码理解

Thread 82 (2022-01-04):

请教一下.exe和dll也算开源吗，那是不是Windows也是开源操作系统了？

LordCasser, 2022-01-04:

peng-zhihui, 2022-01-04:
眼睛不用可以捐给有需要的人，“仓库里有dll”等于“仓库里只有dll”？Firmware里面完整代码看不到？仓库代码统计看不到？
C 94.3% C++ 3.8% ASP.NET 1.5% Other 0.4% ？
仓库README说明看不到？
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

peng-zhihui, 2022-01-04:
我也可以选择不上传exe，你去用license 3万一个的roboDK就是了，上传自己做的免费软件给你用你还白嫖出优越感了？代码核心都在控制器固件和驱动器固件里，我都完全开源了你视而不见？一个上位机就是个GUI壳子你搁这避重就轻是想带什么节奏？

peng-zhihui, 2022-01-04:
你还“trying to get better at Hardware”，所以仓库的完整Hardware源文件你看都不看一眼？眼里就只有那几个DLL了？除了找茬我想不出你提这个issue别的理由啊

LordCasser, 2022-01-04:
1. 其他事情做的好，不能掩盖上位机做法错误问题
2. 最初视频中声称演示所用上位机完全自己开发，将会开源，但是视频中的是roboDK
3. README中的《关于上位机》最初半点没提到，可以理解为补救措施
4. 对自己实现上位机的质疑，申称会开源，开源在何处？
5. 开源不是给狗或者乞丐丢骨头，爱开不开，没人逼着你开源，　开源　！＝　施舍
6. 至于白嫖，不好意思，我根本不用
7. ”因为有功能要添加所以添加好了才开源“，完全站不住脚，大可以开源出来大家一起完成，这才是开源的意义，难不成是代码有问题，比如注释没删干净？

peng-zhihui, 2022-01-04:
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

我也没说上位机要开源啊，你编的？还是你想象的？功能添加完了我也不会开源

“README中的《关于上位机》最初半点没提到，可以理解为补救措施”，你是看不到Update日期？3个月前就上传并更新readme了，眼睛可以多用用。
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

你不用那就更说明你就是找茬的动机了啊，你不用有的是人用，很多人觉得受益不包括你，开源不是给狗的那你又不用还硬贴过来是想表达啥？

peng-zhihui, 2022-01-04:
另外所谓的“最初视频中声称演示所用上位机完全自己开发，将会开源，但是视频中的是roboDK”，也是你编的？
原话是“我也开发了自己的上位机”，要不要去再仔细看看视频？何况我买了RoboDK的license，基于它二次开发了driver，算不算开发？视频里有没有说“完全自己开发”几个字？

peng-zhihui, 2022-01-04:
> “开源不是给狗或者乞丐丢骨头，爱开不开，没人逼着你开源，　开源　！＝　施舍”

你搁这精神分裂呢？提这个issue就是在质疑为啥上位机不开源，到这里又说爱开不开没人逼，这逻辑我也是服。

你怎么不去质疑为啥RoboDK不开源啊，开源出来大家一起完善不是更好吗？还收几万块钱的license，说不定是因为里面也有代码注释没删干净吧对不对？

LordCasser, 2022-01-04:
遣词用句上我不太严谨，见谅
至于去搜寻证据来驳斥，或者玩文字游戏，我没有功夫，但是有很多有闲的人已经去做了，好像那种话题下你就不回复了？
视频剪辑的很精致，全程未露上位机软件标识，一边用一边说，”我也开发了类似于RoboDK的DummyStudio”，有人质疑后才说自己开发的未达标，视频演示用的RoboDK
文字游戏怎么玩都可以，但那是政客的把戏，不该是追求技术的人的手段

peng-zhihui, 2022-01-04:
> 遣词用句上我不太严谨，见谅 至于去搜寻证据来驳斥，或者玩文字游戏，我没有功夫，但是有很多有闲的人已经去做了，好像那种话题下你就不回复了？ 视频剪辑的很精致，全程未露上位机软件标识，一边用一边说，”我也开发了类似于RoboDK的DummyStudio”，有人质疑后才说自己开发的未达标，视频演示用的RoboDK 文字游戏怎么玩都可以，但那是政客的把戏，不该是追求技术的人的手段

是啊，做技术的关注技术就行了，这个项目95%的内容在结构设计，在控制算法，在硬件电路，上位机占比不到5%，视频里也就出现了十多秒钟，而你却只关注到这一个地方，到底是谁在带节奏你看不出来？你是搞技术的，有人是搞事情的，被当做枪使了而且你还信以为真。

抠字眼的是那些人，我上传视频分享作品一不带货二不卖课，还绝大部分完整开源，而有的人却只知道吹毛求疵找茬。硬要找茬的话你一句话超过10个字我就可以找出bug，比如“开源不是给狗或者乞丐丢骨头，爱开不开”，要是有人想搞事情是不是可以给你扣个帽子说你暗示其他用开源的人是狗？这有意思吗？

zhaihao118, 2022-01-04:
> 遣词用句上我不太严谨，见谅 至于去搜寻证据来驳斥，或者玩文字游戏，我没有功夫，但是有很多有闲的人已经去做了，好像那种话题下你就不回复了？ 视频剪辑的很精致，全程未露上位机软件标识，一边用一边说，”我也开发了类似于RoboDK的DummyStudio”，有人质疑后才说自己开发的未达标，视频演示用的RoboDK 文字游戏怎么玩都可以，但那是政客的把戏，不该是追求技术的人的手段

没必要这么较真，上位机只是一小部分，而且核心逻辑在固件中都有，视野放宽点。

peng-zhihui, 2022-01-04:
>

不只是RoboDK，视频中Altium designer、Fusin360我都没有露出软件名称，什么是广告嫌疑你懂吗？何况花了钱买的软件我爱怎么用就怎么用有义务宣传吗？

peng-zhihui, 2022-01-04:
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

peng-zhihui, 2022-01-04:
> >
>
> 不只是RoboDK，视频中Altium designer、Fusin360我都没有露出软件名称，什么是广告嫌疑你懂吗？何况花了钱买的软件我爱怎么用就怎么用有义务宣传吗？

质疑别人误导的同时自己却坚定地做着误导别人的事情，为什么你说的那些搜寻证据来驳斥的人发帖都要匿名+筛选评论你心里没点数？

peng-zhihui, 2022-01-04:
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

HSqure, 2022-01-04:
> 遣词用句上我不太严谨，见谅 至于去搜寻证据来驳斥，或者玩文字游戏，我没有功夫，但是有很多有闲的人已经去做了，好像那种话题下你就不回复了？ 视频剪辑的很精致，全程未露上位机软件标识，一边用一边说，”我也开发了类似于RoboDK的DummyStudio”，有人质疑后才说自己开发的未达标，视频演示用的RoboDK 文字游戏怎么玩都可以，但那是政客的把戏，不该是追求技术的人的手段

不会好好说话我来教教你吧，比如你说的“玩文字游戏”，但凡开始扣帽子了，就已经不在正常讨论的范畴里了，既然不想好好讨论，就别一本正经装讨论浪费大家时间了，这社区没你会更美好。

CaoZengxu, 2022-01-04:
> 最初标题“请教一下.exe和dll也算开源吗，那是不是Windows也是开源操作系统了？” 叙述有误，特此道歉 至于本项目的其他问题，本人对线经验浅薄，前期证据收集不足。无法挑战历经考验，对线经验极其丰富的“peng-zhihui”，也不想浪费时间去玩文字游戏。 我做不到的事情，欢迎大家一起完成，如果有人补充证据，欢迎在此发布，该ISSUE不会关闭
>
> **peng-zhihui** ：我也不会关闭这个ISSUE，大家公正评价就行。**“预设一个立场和结论，然后再去找证据；能有理有据说事实=对线经验极其丰富”**，这大概是很符合你的开源精神和诚信理念的。 顺便我帮你把这个ISSUE置顶了。

你自己主张的自己不举证，全称凭空捏造张口就来。还这么理直气壮的让别人帮你找 牛的🐮

HSqure, 2022-01-04:
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

笑死，经典卖惨“我弱我有理”：“嘤嘤嘤，我虽然没有证据，但是可以让大家帮弱小无力的我找找”（谁理他啊）

CRYOSTATx, 2022-01-04:
” 文字游戏怎么玩都可以，但那是政客的把戏，不该是追求技术的人的手段 “ ，那请问你又是在干什么？ 凭空捏造，张口就来是你所谓技术人的手段？ 可笑至极！

LordCasser, 2022-01-04:
https://www.zhihu.com/answer/2161285400

andy003, 2022-01-04:
> https://www.zhihu.com/answer/2161285400

所以，你想表达的是什么？
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
要不你资助点经费，把这个项目再打磨打磨？

andy003, 2022-01-04:
> https://www.zhihu.com/answer/2161285400 感谢置顶，诸多问题已经有人分析，期待一一批驳，至于文字游戏，图中显而易见 最初标题“请教一下.exe和dll也算开源吗，那是不是Windows也是开源操作系统了？” 叙述有误，特此道歉 至于本项目的其他问题，本人对线经验浅薄，前期证据收集不足。无法挑战历经考验，对线经验极其丰富的“peng-zhihui”，也不想浪费时间去玩文字游戏。 我做不到的事情，欢迎大家一起完成，如果有人补充证据，欢迎在此发布，该ISSUE不会关闭 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
>
> **peng-zhihui** ：我也不会关闭这个ISSUE，大家公正评价就行。**“预设一个立场和结论，然后再去找证据；能有理有据说事实=对线经验极其丰富”**，这大概是很符合你的开源精神和诚信理念的。 顺便我帮你把这个ISSUE置顶了。

话说这不是个技术交流的地方？你觉得哪个地方，做的不好，可以自己做个，让大家膜拜膜拜。

peng-zhihui, 2022-01-04:
> https://www.zhihu.com/answer/2161285400

是的这就是我说的，“匿名+精心筛选评论的帖子”啊，黑子的钱赚得心安理得？你也就信信这样的言论了吧，放着众多理性评价的回答不看，选择性失明好不容易挑出一个抹黑的帖子拿来秀，需要靠各种动机揣测证明你的观点？

HSqure, 2022-01-04:
> https://www.zhihu.com/answer/2161285400
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

REFERENCES:
[1]. 弹幕
[2]. 弹幕
[3]. 网友评论
[4]. 网友评论

andy003, 2022-01-04:
> https://www.zhihu.com/answer/2161285400

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

@LordCasser 这位大佬，不用再纠结上位机是否开源了，你在这里找“证据”的时间，还不如花点时间学下C#或者QT，两周把这个上位机搞定？

peng-zhihui, 2022-01-04:
嗯欲加之罪要找茬很容易的。FOC视频里我一是提了有参考ODrive和VESC，但他们会再强调一遍这是参考开源项目的，说得好像你就是故意的一样；ODrivetool他们大概自己跑都没跑过，看着界面一样就说你是抄的，殊不知原版仓库是几年前发的现在连协议都不兼容了软件根本跑不起来，而我是参考它的Qt UI文件底层全部自己改掉才用起来的；所有项目开不开源，部分开源还是全部我都是明确说明的，FOC那个我有说过开源吗？仓库已经开源的FOC-Lite你倒是去看看啊，选择性失明和装睡的人我也是佩服的。

msnh2012, 2022-01-04:
人红是非多，或许一切都是开源惹的锅，如果一开始不说开源，就当节目看来也挺好.

peng-zhihui, 2022-01-04:
> 人红是非多，或许一切都是开源惹的锅，如果一开始不说开源，就当节目看来也挺好.

是啊，如果都是些这样的人也许还是不开源比较好

Jzacky, 2022-01-04:
> > 人红是非多，或许一切都是开源惹的锅，如果一开始不说开源，就当节目看来也挺好.
>
> 是啊，如果都是些这样的人也许还是不开源比较好

不要啊，不要被这种人影响心情，跟着你做了很多项目，还想继续向您学习呢

LordCasser, 2022-01-04:
对对对，都是迫害，都是子虚乌有，当没摆出东西来的时候，攻击没摆出东西，摆出来了就是人红是非多
为什么不想想作为成名作的自行车项目没人说，其他项目被拔了一堆皮下来？

LordCasser, 2022-01-04:
> > https://www.zhihu.com/answer/2161285400
>
> 是的这就是我说的，“匿名+精心筛选评论的帖子”啊，黑子的钱赚得心安理得？你也就信信这样的言论了吧，放着众多理性评价的回答不看，选择性失明好不容易挑出一个抹黑的帖子拿来秀，需要靠各种动机揣测证明你的观点？

那请一一驳斥，当驳斥不了的时候扣上帽子，打入另类，这种行为只能证明心虚和确有其事
抄开源不标注的时候申称自己是业余主播，难免没注意和疏漏，被扒皮时候就是黑你能赚钱，请问怎么通过黑一个业余主播赚钱？

peng-zhihui, 2022-01-04:
> 那请一一驳斥，当驳斥不了的时候扣上帽子，打入另类，这种行为只能证明心虚和确有其事 抄开源不标注的时候申称自己是业余主播，难免没注意和疏漏，被扒皮时候就是黑你能赚钱，请问怎么通过黑一个业余主播赚钱？

这不是有人驳斥了吗，你也看看兼听则明啊：https://www.zhihu.com/question/491080130/answer/2165261035

我主业是AI工程师，不是业余难道是全职UP？
请问你这摆出来的不都是“动机揣测”吗？有理有据的话需要“匿名”+“精选评论”？所谓“一堆皮”除了你说的机械臂上位机（我自己实现了）和FOC（我实现并且开源了），还有啥？3年前做的plotclock？这东西我可就是写了个教程连视频都没做啊？另外成名作也不是自行车谢谢，量子计划小电视有人说了吗？HoloCubic？PocketLCD呢？仓库还有几十个开源项目呢你也没说啊。

Alansortorz, 2022-01-04:
不要被这些人影响心情，有啥事不能好好说，非要上来就夹带攻击的语调，如果不是动了某些人的蛋糕，那就是心态有问题，纯粹想杠。

Mazeqi, 2022-01-04:
呜呜呜 支持稚晖君

LongtsingLiao, 2022-01-05:
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

稚晖对你关于开源的质疑都已经全部回复了，但你却到现在坚持给他扣个违背开源协议的帽子，而且在这个issue下有恶意言语攻击别人，而不是正常的技术交流，我想不通你不是引战的还能干啥，不要继续回复了好吗？浪费别人的时间，来github提issue的大多是想要交流技术的人，想引战别在这继续了，还我们一个干净的社区，好吗，别脏人了，太恶心了

iamike, 2022-01-05:
其实，看到你们在争论，我突然有个感觉：🤔
1. 🧬基因编辑工程……
2. 🤖工程机械军事装备……
3. 📞通讯设备数据库技术……
4. ……
💡结论：碳基生命(自私的基因) VS 硅基生命(彻底开源)
从哲学角度来看碳基生命为了基因的延续，必然会采取主动措施进行保护。其实，这也不是什么坏事，但是最终我们可能最终走向硅基生命吗？比如元宇宙😶‍🌫️🤯

mailonghua, 2022-01-06:
个人觉得，开源本身就是一个令人钦佩的精神，能从中学到很多知识，能够快速进步，这是一件非常有意义的事情，所以请不要吹毛求疵，鸡蛋里挑骨头的去刷存在感。请尊重别人的开源和努力。

iamike, 2022-01-06:
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
哈萨克斯坦又闹了，乌克兰和俄罗斯也闹矛盾，以前好好的一个社会主义大家庭👪，怎么就。。。。。变成今天这样

guguobao, 2022-01-12:
支持稚晖君

guguobao, 2022-01-12:
支持稚晖君 +1

cjx666666, 2022-01-18:
支持稚晖君 +2

NM2012, 2022-02-10:
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

又没要你看，不爽去别的地方。再说你不服你也整个出来给我们看看！

fanxing-6, 2022-03-14:
啊这, 怎么到处都有魔怔人, 没事找事....

845184278, 2022-03-16:
这不是技术人员逛的地方吗？这都是魔怔了

HeYongxian, 2022-04-27:
支持彭老师！

chi-xinming, 2022-06-23:
哇靠 这都有小黑子

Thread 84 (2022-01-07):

驱动校准和REF通讯问题

learner-f, 2022-01-07:
关于电机校准部分

1. 烧录您直接提供的固件，按下KEY1 KEY2上电，电机进行正反方向运动，过程需长按按键否则运动终止，结束后，电机轴和未上电时是同样状态，重新上电重复上述操作，电机不再运动

2. 通过CLION直接编译烧录，短按KEY1 KEY2上电，电机就可以完成运动，结束后，可以外力转动电机出轴但能明显感受到阻力，且断电后重复按KEY1 KEY2上电，电机可再次运动

想问一下哪个是正常情况，若两者都有问题，希望大佬能指明应该是怎样的效果

与REF连接后，通过命令行发送...joint_1.do_calibration()命令，电机没有反应
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
芯片序列号已经通过修改程序，调试电机ID为1，除此之外，程序还有需要结合硬件调整的地方吗
程序逻辑梳理过了，细处不知从何入手，希望大佬能提供个解决思路，感谢

peng-zhihui, 2022-01-07:
1.应该都是正常的，电机校准完会自动重启，而上电不给指令的话是不会进入使能状态的（除非设置了enable_on_boot），所以你要通过CAN发送任意指令（位置、速度、力矩）才能让电机使能。
2.检查CAN是否连接正确（CAN1不是CAN2），终端电阻加了没（120R）

peng-zhihui, 2022-01-07:
另外不要用ODriveTool连接REF，协议不通用的，我新上传一个CMD根据你再试试

peng-zhihui, 2022-01-07:
电机你可以修改一下代码，在main.cpp里面用代码给一个速度指令来测试，具体指令函数可以参考can_protocol里面的内容

learner-f, 2022-01-14:
大佬你好，还有些问题请教

1. 最开始对源码直接编译时出了些错误，是mt6816_base.h和tb67h450_base.h文件中“端口指定工具”部分下的函数出现了“功能未实现”的错误
于是我在两个文件同名的CPP文件中重新添加这些函数，程序能正常编译了，但不知道这种方式会不会导致某些功能出错

2. ODrivetool中可以读取到REF的一些参数信息比如ID、温度等，所以“协议不通用”指的是对电机指令控制部分吗

3. 驱动校准后，按键1、2不能执行相应功能，这种情况貌似可以用issue#85中的内容解释，具体原因就不清楚了

关于硬件的部分已经检查过了，没有遗漏的地方
问题有些琐碎，见谅

peng-zhihui, 2022-01-17:
1. 把未实现的函数设置为纯虚函数就行（加上"=0"），应该是你的编译器问题。
2. 是的，电机协议是自定义的，跟odrivetool用的都是fibre实现所以底层基础协议通用但是上层应用协议不一样
3. 程序覆盖的问题我在issue#85回答了你再试一下，如果编译出的固件尺寸没问题应该就可以用了，或者你用我预编译的先测试一下（记得CAN要加终端电阻）

jzijin, 2022-04-13:
>

稚晖君，你好。我当前也是REF连接电机驱动板调试。CAN通信失败，电机驱动板没有收到消息。
关于终端电阻，我看原理图上是都没有加终端电阻的。不加终端电阻是否会影响到CAN通信呢？

jzijin, 2022-04-13:
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

你好。请问下后面这个问题解决了吗？是怎么解决的？望解答，感谢。

Joelliamliu, 2022-08-08:
>

我的Dummy Studio跟核心板通讯一直有问题，显示能链接，有send信息但一直无receive信息，需要我下载Odrive安装吗？ 怎么才会出现Reconnected to Dummy-Robot 3055385E3030 as dummy0这条信息（我的显示
![Uploading WeChat Image_20220808170223.jpg…]()
NameError: name 'dummy' is not defined）？谢谢

peng-zhihui, 2022-08-08:
用zadig安装libusb驱动，ref interface2那个设备替换为libusb驱动

Joelliamliu, 2022-08-09:
> 用zadig安装libusb驱动，ref interface2那个设备替换为libusb驱动

已经安装libusb驱动，但Dummy Studio和REF主板通讯依然有问题
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

peng-zhihui, 2022-08-09:
这个usb是reftool的命令行连接的，不是dummystudio，studio用的就是普通串口

Joelliamliu, 2022-08-09:
> 用zadig安装libusb驱动，ref interface2那个设备替换为libusb驱动

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

spacomp, 2022-08-18:
> Dummy Studio可以和REF通信了吗？

Joelliamliu, 2022-08-20:
> > Dummy Studio可以和REF通信了吗？

已经连接上，但通讯有问题，我正在找原因

ZXYZZP, 2022-08-26:
>

请问找到原因了吗我的显示usb已连接但没接收到数据，发送数据也没反应

ZXYZZP, 2022-08-26:
> Joelliamliu

请问找到原因了吗我的也是usb连接成功但没接收到数据，发送数据也没反应

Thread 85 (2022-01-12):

步进电机驱动器build出来的固件有119KB，无法再保存32K的编码器校验数据！

real-jianhua, 2022-01-12:
现在的代码build出来的固件有119K那么大，已经没有空间保存校验数据了，导致编码器校准后执行保存时把自身的固件给破坏了，程序重启后就没法正常工作了。

learner-f, 2022-01-13:
是电机校准之后就没有其他反应了吗，包括按键什么的

real-jianhua, 2022-01-13:
是的，固件被破坏了，无法正常工作了。

peng-zhihui, 2022-01-13:
我上一个提交应该就是修复这个问题了，你pull一下最新代码看看

real-jianhua, 2022-01-13:
我就是用最新提交的代码编译的了，目前这个代码编译出来的固件太大了，大约118K，我用烧录软件检查过烧录到stm32后，占用了0x8000000到0x801D8D0的空间，而编码器写入数据的起始地址是0x08017C00。这样保存编码器数据的话会把原来的固件破坏掉，保存重启后驱动器就没法正常工作了。

real-jianhua, 2022-01-13:
我就是用最新提交的代码编译的了，目前这个代码编译出来的固件太大了，大约118K，我用烧录软件检查过烧录到stm32后，占用了0x8000000到0x801D8D0的空间，而编码器写入数据的起始地址是0x08017C00。这样保存编码器数据的话会把原来的固件破坏掉，保存重启后驱动器就没法正常工作了。

NM2012, 2022-01-15:
问下这个这个步进电机的代码是什么平台编译的？

peng-zhihui, 2022-01-16:
> 现在的代码build出来的.bin文件固件有119K那么大，已经没有空间再保存编码器的校验数据了，导致编码器校准后执行保存时把自身的固件给破坏了，程序重启后就没法正常工作了。

清除CMake缓存重新编译一下，我这边修复后是可以的：
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

StudenLin, 2022-03-06:
> 现在的代码build出来的.bin文件固件有119K那么大，已经没有空间再保存编码器的校验数据了，导致编码器校准后执行保存时把自身的固件给破坏了，程序重启后就没法正常工作了。

请问你的电机现在可以正常工作吗？如何查看固件是否被破坏了

Jzacky, 2022-03-23:
> 我就是用最新提交的代码编译的了，目前这个代码编译出来的固件太大了，大约118K，我用烧录软件检查过烧录到stm32后，占用了0x8000000到0x801D8D0的空间，而编码器写入数据的起始地址是0x08017C00。这样保存编码器数据的话会把原来的固件破坏掉，保存重启后驱动器就没法正常工作了。

那几个虚函数后边不要添加=0，否则换了编译器9.2.1编译出来也119，只保证编译器版本程序默认编译就可以了

ZXYZZP, 2022-08-12:
>

我现在也遇到了相同的问题一定要更换编译器版本才有用吗

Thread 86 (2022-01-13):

PCB 元器件焊接

fumingxi, 2022-01-13:
按PCB文件中的BoM找厂家焊接，发现有几个元器件对不上。。

本人硬件小白，有哪位大神成功焊出来板子的能分享下打板焊接渠道嘛？

learner-f, 2022-01-13:
嘉立创可以打板，淘宝上就能找到，贴片应该也可以，具体可以问客服，不过自己贴片的比较多吧

fumingxi, 2022-01-13:
> 嘉立创可以打板，淘宝上就能找到，贴片应该也可以，具体可以问客服，不过自己贴片的比较多吧

大佬在他家打的么？因为没有焊接设备所以想找一家能提供一站式服务的。

learner-f, 2022-01-13:
我是在他家打的板，比较便宜，贴片等其他服务应该不能直接在淘宝下单，需要在官网或下载app，具体怎么操作问客服就行

fumingxi, 2022-01-13:
> 我是在他家打的板，比较便宜，贴片等其他服务应该不能直接在淘宝下单，需要在官网或下载app，具体怎么操作问客服就行

谢大佬，我问下能不能提供贴片服务。

Meieryang, 2022-02-18:
我昨天在嘉立创免费打板的时候，看见有个SMT选项，那个是不是就是你说的帮忙贴片啊

fresh-000, 2022-03-04:
嘉立创可以提供贴片服务，不过回来得好好检查，之前实验室五块板子两块焊接出了点小问题

BillCai06, 2022-05-23:
0402 真的太小了

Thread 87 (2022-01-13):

> 可以可以可以 联系方式？ 从 Windows 版邮件发送 发件人: fumingxi 发送时间: 2022年1月13日 16:02 收件人: peng-zhihui/Dummy-Robot 抄送: echoes; Manual 主题: Re: [peng-zhihui/Dummy-Robot] 关于电机的型号和详细的购买地址有吗？ (Issue #62) 请问有谐波减速器的型号吗 我人在国外购买比较方便 CSF-8-30-1U CSF-5-30-1U — Reply to this email directly, view it on GitHub, or unsubscribe. Triage notifications on the go with GitHub Mobile for iOS or Android. You are receiving this because you are subscribed to this thread.Message ID: ***@***.***>

echoeswang, 2022-01-13:
> 可以可以可以 联系方式？ 从 Windows 版邮件发送 发件人: fumingxi 发送时间: 2022年1月13日 16:02 收件人: peng-zhihui/Dummy-Robot 抄送: echoes; Manual 主题: Re: [peng-zhihui/Dummy-Robot] 关于电机的型号和详细的购买地址有吗？ (Issue #62) 请问有谐波减速器的型号吗 我人在国外购买比较方便 CSF-8-30-1U CSF-5-30-1U — Reply to this email directly, view it on GitHub, or unsubscribe. Triage notifications on the go with GitHub Mobile for iOS or Android. You are receiving this because you are subscribed to this thread.Message ID: ***@***.***>

了解了一下HD家的产品是B2B的，得找专业的订货公司订货才行，现在这两个减速器订货周期已经排到12个月了，原价4000左右。可以考虑自己修改方案或者换别家的谐波减速器，也可以等zhihui君出简易版dummy

_Originally posted by @Burnwhite in https://github.com/peng-zhihui/Dummy-Robot/issues/62#issuecomment-1012232134_

peng-zhihui, 2022-01-17:
国内有一家做迷你谐波的厂家有同型号仿品，闲鱼搜迷你谐波减速可以找到，价格大概一千多一个。不过对精度力矩要求没那么高的话还是建议等dummy青春版，里面减速器是自制的成本几十块钱就够了。

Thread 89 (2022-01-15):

重力补偿问题

w-1016-Papman, 2022-01-15:
博主大大您好，看到您做的小型机械臂，非常好奇您是如何解决机械臂的重力补偿问题的，因为我想的是：在实际应用过程中，除开机械臂自身的重力力矩需要补偿，还有一些非几何误差是不易测量并且不易线性化的（比如连杆的形变、关节的柔性以及电机本身的精度阈值等等因素导致的末端执行器与l理论位置出现偏差），我已经想这个问题大概想了两周了，但很遗憾，我有点笨，所以来这里向您提问，希望您在看到这一问题时，能劳神帮我解答一二，感激不尽。预祝新年快乐！   

                                                                                                                                             ——   一名来自天津的大二本科生

peng-zhihui, 2022-01-17:
实际的机械臂零力拖拽主要就是消除两项：重力和摩擦力，因为拖动速度比较慢所以惯性力可以忽略；摩擦力可以认为只跟每个关节转速有关，重力要复杂一些，靠重力力矩回归矩阵描述，相关参数都需要做系统辨识通过最小二乘法标定出来，可以自己去搜一下相关资料和论文看。我这个项目里因为自重很轻，重力项是通过选取合适的减速器减速比靠静摩擦力矩平衡的。

msnh2012, 2022-01-19:
其实你说的末端和实际理论的误差，其实除了收到重力的影响之外，本身机械误差也是无法忽视的。一般来说，每台机械臂的DH参数都是不一样的，在出厂之前都需要使用激光跟踪仪来重新拟合DH参数。重力项对Dummy的影响不是很大，本身其负载也比较小，当然对于工业大负载的臂的话，重力，库伦摩擦力，惯性矩是需要通过参数辨识的，一般每个厂商都有自己一套标准的方法。当然做这些的前提的话，是需要一个不错的电机和减速器的，硬件不行的话，算法硬刚也是不行的。对于电机的话一般是PMSM搭配FOC实现精确力矩控制，对于减速器的话一般是谐波或者RV减速器达到小体积，"0"背隙，大减速比，大负载。

w-1016-Papman, 2022-01-19:
> 实际的机械臂零力拖拽主要就是消除两项：重力和摩擦力，因为拖动速度比较慢所以惯性力可以忽略；摩擦力可以认为只跟每个关节转速有关，重力要复杂一些，靠重力力矩回归矩阵描述，相关参数都需要做系统辨识通过最小二乘法标定出来，可以自己去搜一下相关资料和论文看。我这个项目里因为自重很轻，重力项是通过选取合适的减速器减速比靠静摩擦力矩平衡的。

好的，了解了，谢谢您嘞

w-1016-Papman, 2022-01-19:
> 其实你说的末端和实际理论的误差，其实除了收到重力的影响之外，本身机械误差也是无法忽视的。一般来说，每台机械臂的DH参数都是不一样的，在出厂之前都需要使用激光跟踪仪来重新拟合DH参数。重力项对Dummy的影响不是很大，本身其负载也比较小，当然对于工业大负载的臂的话，重力，库伦摩擦力，惯性矩是需要通过参数辨识的，一般每个厂商都有自己一套标准的方法。当然做这些的前提的话，是需要一个不错的电机和减速器的，硬件不行的话，算法硬刚也是不行的。对于电机的话一般是PMSM搭配FOC实现精确力矩控制，对于减速器的话一般是谐波或者RV减速器达到小体积，"0"背隙，大减速比，大负载。

好的好的，谢谢您啦！

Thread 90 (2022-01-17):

Dummy青春版不知道什么时候发布呀

learningintheworld, 2022-01-17:
之前看到说会出Dummy青春版的一个保姆级视频教程，请问出了吗，在哪里可以看

peng-zhihui, 2022-01-17:
没有假期，估计还要两三个月完成...

Eddie-717314-Huang, 2022-02-01:
很期待！ 🙏

zhoufeng512, 2022-03-14:
> 没有假期，估计还要两三个月完成...

把我假期匀给你😀

kaine380, 2022-04-25:
>

期待催更催更😣

CGY11, 2022-05-09:
我假期给你！！

zhoufeng512, 2022-10-06:
鸽王名不虚传

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

HTensor, 2022-11-05:
咕咕咕

quantingxie, 2023-07-19:
Hi, is the new dummy version released?

zhoufeng512, 2023-08-14:
仨月三月又三月, 关注这个项目的时候我女还在上幼儿园, 一转眼, 马上三年级了...

Stat2000, 2024-01-29:
> 没有假期，估计还要两三个月完成...

24年了，铁粉前来催更[doge]

HuangDDU, 2024-07-14:
Dummy青春版期待中...

hongzhuoxx, 2024-07-20:
Dummy青春版 还有机会吗。。。

lyfiiu, 2025-02-24:
大一机械专业想复刻一下，25年会更吗

CoderSuHang, 2025-02-24:
您好，我是苏航，感谢您的来信！我会尽快对来信进行查看并尽快给您进行回复，祝您身体健康，工作顺利，谢谢！

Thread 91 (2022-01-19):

TRJ轨迹跟踪控制算法做了吗？

m986883511, 2022-01-19:
您在Readme中写支持TRJ轨迹跟踪
，我想参考您的实现，我找到比较像的是如下代码？是空的啊，是我找错了吗？
麻烦指导一下。

void DummyRobot::MoveTrajectoryJ(float _j1, float _j2, float _j3, float _j4, float _j5, float _j6)
{

}

void DummyRobot::MoveTrajectoryL(float _x, float _y, float _z, float _a, float _b, float _c)
{

}

peng-zhihui, 2022-01-19:
轨迹插值有一部分实现在驱动器内，控制器里面这个轨迹只做线性插值用于在两个MoveL指令间插值扩充指令频率到200Hz，另外这块我写完了还没时间测试，验证完成了会更新上来。

m986883511, 2022-01-19:
期待您的更新

m986883511, 2022-01-21:
在驱动器中的实现的线性插值代码，能指明一下在哪里吗？

还有一点建议：由于目前没有实现TRJ轨迹控制，建议您在Readme中标注位为 Todo。

peng-zhihui, 2022-01-21:
轨迹规划都在 `2.Firmware\Ctrl-Step-Driver-STM32F1-fw\Ctrl\Motor\motion_planner.cpp`文件里；意见已采纳
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

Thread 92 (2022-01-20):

在编译步进电机驱动的时候报错！理论应该是链接的时候出错。

li460135301, 2022-01-20:
PULL了最新版本的，重置过CMAKE，好像问题依旧存在。，且空间也没有变小，这个是是哪里设置错了吗？主控的代码是正常的！非常感谢！
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

peng-zhihui, 2022-01-20:
很可能是gcc版本问题，切换到9.2.1试试

li460135301, 2022-01-20:
> 很可能是gcc版本问题，切换到9.2.1试试

确实，gcc-arm-none-eabi更换为9.2.1之后正常了，非常感谢！

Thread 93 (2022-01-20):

麻烦稚晖君贴上相关零件（尤其是电机）的购买链接，谢谢！

Lixuannan, 2022-01-20:

fumingxi, 2022-01-21:
PCB零件都在工程里面标注了。电机型号在step文件里也有。淘宝都能搜到

peng-zhihui, 2022-01-21:
零件太多了，去淘宝或者立创一个一个找就行，电机就是普通的20步进和42步进，前者大概40一个，后者20一个

SWEETNESSOWO, 2022-01-28:
求谐波减速器的购买连接>_<

Burnwhite, 2022-01-29:
> 求谐波减速器的购买连接>_<

我有几个多的

Lixuannan, 2022-02-07:
谢谢

Closed 2022-02-07.

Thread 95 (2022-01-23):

关于tb67h450_base.h

wztted, 2022-01-23:
tb67h450_base.h文件里好几个private函数都没有实现是怎么回事？？？

peng-zhihui, 2022-01-23:
复习一下c++基础，这是基类虚函数。

wztted, 2022-01-23:
> 复习一下c++基础，这是基类虚函数。

非常感谢大佬这么快回复（受宠若惊），是不是纯虚加上=0才可以？不然总报错。我是机械专业，在汽车行业已浸淫十年，这两年一直业余时间学习嵌入式方面的东西（单片机，PCB设计，C++），前年用stm32单片机做了一个魔方恢复机器人（抖音1704469178）。去年看到大佬的机械臂视频崇拜得五体投地，把你所有的视频都撸了一遍，准备亲手复现这个机械臂，希望实在搞不懂的时候能求助大佬，毕竟大佬日理万机。

zhenghengju, 2022-03-15:
> > 复习一下c++基础，这是基类虚函数。
>
> 非常感谢大佬这么快回复（受宠若惊），是不是纯虚加上=0才可以？不然总报错。我是机械专业，在汽车行业已浸淫十年，这两年一直业余时间学习嵌入式方面的东西（单片机，PCB设计，C++），前年用stm32单片机做了一个魔方恢复机器人（抖音1704469178）。去年看到大佬的机械臂视频崇拜得五体投地，把你所有的视频都撸了一遍，准备亲手复现这个机械臂，希望实在搞不懂的时候能求助大佬，毕竟大佬日理万机。
我也是编译时 这几个函数报未定义  你最后是怎么解决的

wztted, 2022-03-15:
声明加上=0啊

zhenghengju, 2022-03-15:
>
😅  对了还有这个工程怎么没有.ioc 文件

wztted, 2022-03-15:
> >
>
> 😅 对了还有这个工程怎么没有.ioc 文件

工程本来也不需要IOC啊，你要它干嘛？

zhenghengju, 2022-03-15:
>
难道稚晖大佬本来就没用cubemx吗
看代码应该是用了cubemx 生成，定时器 dma 等等初始化，虽然看代码也能看出怎么配置的，有ioc文件不是方便看吗，而且也更方便修改。主要是对我这样的小白更友好  是不要求太高了😁

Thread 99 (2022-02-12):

关于ref 最新固件和reftool工具的使用求助

StudenLin, 2022-02-12:
稚晖君您好，我尝试了前几天发布的ref v2.0编译通过，烧录后屏幕不亮，但接入usb有反应，电脑识别为ref 1.0 cdc interface，尝试使用reftool发现连接不上，折腾了一天还是不懂怎么弄，求救🆘大佬

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

peng-zhihui, 2022-02-14:
更新前可以连接吗？有没有自己添加额外的RTOS任务？有的话检查一下是否是栈溢出了

peng-zhihui, 2022-02-14:
需要用zadig安装libusb驱动的，你安装过了？

StudenLin, 2022-02-14:
> 需要用zadig安装libusb驱动的，你安装过了？

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

不知道这样子对不对呢

peng-zhihui, 2022-02-18:
对的，那你可能得自己debug一下了

StudenLin, 2022-02-18:
> 对的，那你可能得自己debug一下了

后面选interface 2就可以了，错选了interface 0，小错误浪费了好多时间😂，谢谢您

jzijin, 2022-04-12:
你好，请问下，我在执行run.bat的时候遇到这个问题，有可能是什么原因导致的呢？
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

Joelliamliu, 2022-08-15:
> 对的，那你可能得自己debug一下了
这个ACK：503代表什么信息？
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

ZXYZZP, 2022-08-17:
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
一连接板子就退出进程是什么原因

wastom, 2024-11-24:
> > 对的，那你可能得自己debug一下了
>
> 后面选interface 2就可以了，错选了interface 0，小错误浪费了好多时间😂，谢谢您

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
我选了interface 2还是会断开连接，请问你有遇到过吗

CoderSuHang, 2024-11-24:
您好，我是苏航，感谢您的来信！我会尽快对来信进行查看并尽快给您进行回复，祝您身体健康，工作顺利，谢谢！

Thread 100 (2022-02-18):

请教一下作者关于机械臂的修改

mailonghua, 2022-02-18:
你好，我觉得dummy是一套十分精巧且美观的机械臂
因为现在作者用的这款减速器已经不容易购买，所以想使用行星减速器替换
但是看了提供step文件当中不包含草图，所以不知道如何下手来修改机械结构以适配行星减速器
，我能想到用过自建草图再原有的实体上进行填充\会盲切，但这样好像很麻烦
所以请教一下，该如何进行，希望能得到回复

多谢

mailonghua, 2022-02-18:
> step本身就是可编辑的3D格式，基本所有建模软件都能修改，要修改结构你需要加深一下建模技能，看看相关软件的视频教程吧，就算有草图也不是改几个参数就能适配的，肯定要自己重新设计部分零件。

多谢解答和建议，关于建模确实缺少很多，会多做加强
若是想重新修改一些实体结构，是需要对这个实体重新设计，而不是在原有实体的条件下进行直接修改，不知道这样理解是否正确

Closed 2022-02-23.

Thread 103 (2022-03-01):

关于estVelocity和CompensateAdvancedAngle

wztted, 2022-03-01:
下面这段中的estVelocity没有看明白，还有CompensateAdvancedAngle这个函数补偿的到底是什么？怎么测量函数中的参数？
// Estimate Velocity
    controller->estVelocityIntegral += (
        (controller->realPosition - controller->realPositionLast) * motionPlanner.CONTROL_FREQUENCY
        + ((controller->estVelocity << 5) - controller->estVelocity)
    );
    controller->estVelocity = controller->estVelocityIntegral >> 5;
    controller->estVelocityIntegral -= (controller->estVelocity << 5);

    // Estimate Position
    controller->estLeadPosition = Controller::CompensateAdvancedAngle(controller->estVelocity);
    controller->estPosition = controller->realPosition + controller->estLeadPosition;

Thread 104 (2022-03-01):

PID中的I项代码是不是错了？

wztted, 2022-03-01:
下面这段是不是第四行错了？应该是   config->pid.outputKi += config->pid.integralRound 吧？
    config->pid.integralRound += (config->pid.ki * config->pid.vError);
    config->pid.integralRemainder = config->pid.integralRound >> 10;
    config->pid.integralRound -= (config->pid.integralRemainder << 10);
    config->pid.outputKi += config->pid.integralRemainder;

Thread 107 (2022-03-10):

请问Controller和Dangle影响核心功能吗？

fumingxi, 2022-03-10:
稚晖君好，我这边在尝试复现核心功能，Motor和REF都已经OK了，为了驱动机械臂，我的理解是：
1. Peak主要做交互，不影响功能，使用电脑串口也是可以的？
2. Controller和Dangle非必须，不影响机械臂核心功能？不是很理解这两个板子主要是做什么的

peng-zhihui, 2022-03-10:
1.是的，串口可以，但是更推荐使用仓库的reftool命令行交互方便得多，可以直接调参和控制每一个电机的行为
2.不影响，Controller是视频中演示的无线6轴力反馈手柄（PS5手柄改造的），Dangle是手柄的电脑端接收器

fumingxi, 2022-03-10:
> 1.是的，串口可以，但是更推荐使用仓库的reftool命令行交互方便得多，可以直接调参和控制每一个电机的行为 2.不影响，Controller是视频中演示的无线6轴力反馈手柄（PS5手柄改造的），Dangle是手柄的电脑端接收器
>
> 另外机械臂的标定校准有一些讲究，我平时比较忙，B站上有人已经搞定了，可以跟他交流一下@[江城子1984](https://space.bilibili.com/622926297)

多谢大佬！！！

Closed 2022-03-10.

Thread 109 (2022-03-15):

关于步进电机驱动代码中数字的疑惑

mailonghua, 2022-03-15:
作者你好，最近在看步进电机的驱动代码，但是在类似表示FOC控制的函数中存在疑惑若有空希望能帮忙解惑
1.如下面的将dac_reg*5083,这个5083该如何理解
2.同时想咨询一下，步进电机的软件细分有类似的文章能推荐一下吗，原理不了解，代码理解起来比较困难
非常感谢
_void TB67H450Base::SetFocCurrentVector(uint32_t _directionInCount, int32_t _current_mA)
{
    phaseB.sinMapPtr = (_directionInCount) & (0x000003FF);
    phaseA.sinMapPtr = (phaseB.sinMapPtr + (256)) & (0x000003FF);
    phaseA.sinMapData = sin_pi_m2[phaseA.sinMapPtr];
    phaseB.sinMapData = sin_pi_m2[phaseB.sinMapPtr];
    //dac_reg
    uint32_t dac_reg = abs(_current_mA);
    dac_reg = (uint32_t) (dac_reg * 5083) >> 12;
    dac_reg = dac_reg & (0x00000FFF);_

jzijin, 2022-04-10:
请问下后来解决了吗？5083是什么意思呢？

raulcao, 2022-09-21:
> 请问下后来解决了吗？5083是什么意思呢？

5083 /4096 = 4095/3300

YangAoTeng, 2022-11-26:
(dac_reg * 4095 / 3300)的变种，这一段代码是根据细分来查sin表，决定PWM输出合成的电流，进而控制步进电机的运动。

YangAoTeng, 2022-11-26:
如果这一段实在看不懂的话，可以了解一下步进电机的结构与步进电机细分的原理。 就可以理解清楚了

Closed 2022-03-22.

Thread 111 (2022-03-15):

稚晖君可以给大家解释一下抓手力反馈原理吗？

rcdevice, 2022-03-15:
您视频里有段话说，如果减速比设计的好，步进电机可以反驱？

我想知道反驱是什么原理？

还有，我看了您的抓手电路图，　力反馈原理能讲解一下？也是利用步进电机的反驱原理吗？

原理图中　，　GPIO14 GPIO12  是不是电流检测？  GPIO15 和 GPIO13 这两个电位器，是不是抓手的角度检测？ 和力矩检测有关吗？

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

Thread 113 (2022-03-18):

五相电机 or 两相电机

little-star-bling-bling, 2022-03-18:
大佬，项目里的电机驱动板是驱动两相步进电机的吧？我看模型里有几处用了五相步进电机，驱动板也能通用吗？

peng-zhihui, 2022-03-18:
两相的，5相要改驱动不通用

fumingxi, 2022-03-22:
> 两相的，5相要改驱动不通用

所以step文件中列举的PK543AW-H50S和PK513PA-H50S都被换成了常规的两相电机？

peng-zhihui, 2022-03-22:
是的

StarJi1991, 2022-03-27:
> 两相的，5相要改驱动不通用

但我看了下你做的机械手实物图上末端确实用的是H50S，请问稚晖君当时有写5相的驱动吗？我查了下一般都是2相4线，貌似没有5相的开源驱动

fumingxi, 2022-03-28:
> > 两相的，5相要改驱动不通用
>
> 但我看了下你做的机械手实物图上末端确实用的是H50S，请问稚晖君当时有写5相的驱动吗？我查了下一般都是2相4线，貌似没有5相的开源驱动

稚晖应该是把后面的步进拆掉了，只用了减速。
我也买了这款准备暴力搞掉它。。。

StarJi1991, 2022-04-11:
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

我也买了打算暴力拆解，但是电机和减速器连得很紧啊，兄弟成功了吗？

fumingxi, 2022-04-11:
200多买了个博世的角磨机，磨开的。。。

Closed 2022-04-15.

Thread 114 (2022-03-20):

电机驱动进入使能模式问题

Scoulson986, 2022-03-20:
稚晖君您好，在复刻42电机驱动板的时候我遇到了一点问题，期望您能答复：
驱动板现在可以进入编码器校准模式，电机正反转一圈后使能，阻力很大。但是key1和key2无反应，疑似死机现象。使用Stlink utility连接后阻力消失，key1和key2依然无反应。
检查驱动板焊接时测量了MT6816引脚的电压值，大致如下图所示。
校准完之后的数据似乎也没写入Flash中，在程序里看到MT6816的地址是0x08017C00，但当电机进入上述使能后，用utility看该地址的flash是空的。
后来试图烧录您的hex程序进驱动板，地址是有数据的，但是key1和key2摁下后仍然无反应。

图1（mt6816及其电压值）
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
图二（mt6816地址）
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

peng-zhihui, 2022-03-21:
用我的hex校准过后，不发送指令是不会转的，可以这样测试，按键1按一下解除使能，手动转动电机到任意位置，再按一下按键1使能，电机应该会回到初始位置

peng-zhihui, 2022-03-21:
你自己编译校准失败，应该是flash溢出的问题，翻一下之前的issues，解决办法是改用和我一样版本的GCC编译

Scoulson986, 2022-03-21:
好的，谢谢大佬，我再试试看

jzijin, 2022-04-09:
> 稚晖君您好，在复刻42电机驱动板的时候我遇到了一点问题，期望您能答复： 驱动板现在可以进入编码器校准模式，电机正反转一圈后使能，阻力很大。但是key1和key2无反应，疑似死机现象。使用Stlink utility连接后阻力消失，key1和key2依然无反应。 检查驱动板焊接时测量了MT6816引脚的电压值，大致如下图所示。 校准完之后的数据似乎也没写入Flash中，在程序里看到MT6816的地址是0x08017C00，但当电机进入上述使能后，用utility看该地址的flash是空的。 后来试图烧录您的hex程序进驱动板，地址是有数据的，但是key1和key2摁下后仍然无反应。
>
> 图1（mt6816及其电压值） 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 图二（mt6816地址） 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

请问下，这个问题后来解决了吗？是怎么解决的？

Scoulson986, 2022-04-09:
这个问题最后解决了。说一下解决的方法，就是烧录完成之后使用debug模式，一步步运行，直到进入if条件(if button1和button2 pressed的条件）后，摁住key1，key2，继续运行，然后电机开始校正，继续单步运行直到完成一遍程序后，断电重启即可进行使能切换了。研究这个过程花了好长时间，最后推测可能是编译器版本原因或者环境配置和稚晖君的稍有出入，导致出现这个问题。

Closed 2022-04-09.

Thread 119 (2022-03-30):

固件下载无法识别芯片

fumingxi, 2022-03-30:
用ST-Link v2 接42驱动板的GND, CLK, DIO, 板子供3.3v电还是无法找到target.
原理图中有boot 0但是没找到引脚噢。。
第一次下载固件是需要通过两个按键来进入flash模式吗？

求刷成功的大佬指点。

peng-zhihui, 2022-03-30:
不需要，检查电路焊接，也可能买到国产假芯片了

fumingxi, 2022-03-31:
> 不需要，检查电路焊接，也可能买到国产假芯片了

好的，谢谢大佬回复

Closed 2022-07-11.

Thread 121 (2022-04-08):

断电重启，电机驱动板无法正常运行

jzijin, 2022-04-08:
Hi，稚晖君：
请问下，有遇到过电机驱动板在烧录器烧录完之后可以正常运行，但是只要断电重启之后就无法正常运行的情况吗？

jzijin, 2022-04-08:
请问下电机驱动代码中，EXTI9_5_IRQHandler中断函数，为什么需要return之后在执行HAL_GPIO_EXTI_IRQHandler操作呢？
```
void EXTI9_5_IRQHandler(void)
{
  /* USER CODE BEGIN EXTI9_5_IRQn 0 */
    return;
  /* USER CODE END EXTI9_5_IRQn 0 */
  HAL_GPIO_EXTI_IRQHandler(GPIO_PIN_7);
  /* USER CODE BEGIN EXTI9_5_IRQn 1 */

  /* USER CODE END EXTI9_5_IRQn 1 */
}
```

peng-zhihui, 2022-04-08:
应该是因为你编译的文件尺寸超过了flash设置的app区，导致校准之后数据覆盖了代码，参考issues里面另一个类似问题，替换gcc版本解决

jzijin, 2022-04-09:
> 应该是因为你编译的文件尺寸超过了flash设置的app区，导致校准之后数据覆盖了代码，参考issues里面另一个类似问题，替换gcc版本解决

稚晖君，你好。我debug的时候，发现掉电重启之后，频繁的走到了EXTI9_5_IRQHandler函数中，所以系统卡死了。我将return和HAL_GPIO_EXTI_IRQHandler交换顺序就好了。不知道这是为啥。

peng-zhihui, 2022-04-09:
那是IO信号的中断，这板子上没用到，直接删掉就行

Closed 2022-04-10.

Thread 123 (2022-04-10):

步进电机校准失败

jzijin, 2022-04-10:
稚晖君，你好：
        我调试电机驱动板的时候发现，校准老是失败。我在OnUartCmd中添加控制校准的代码。上电后通过串口发送'C' 校准电机。当电机正转两圈反转两圈后，检查校准数据失败，CalibrationDataCheck的返回值是CALI_ERROR_AVERAGE_DIR。请问下有可能是什么原因导致的呢？
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

驱动板和电机的连接是这样的：
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

peng-zhihui, 2022-04-11:
你都没接磁铁和编码器，校准怎么可能成功呢...驱动板是贴在点击后面的，电机轴上要安装一个径向充磁的磁铁

Closed 2022-04-13.

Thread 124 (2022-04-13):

CAN总线通信

jzijin, 2022-04-13:
稚晖君，你好：
当前调式，REF板通过CAN连接了一个电机驱动板。通过您提供的CLI_tool发送校准指令给电机驱动板，但是电机驱动板并没有反应。REF板单步调试的情况来看，走到了CanSendMessage发送数据了。请问下有可能是什么原因导致的呢？
以下是连接图：
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

jzijin, 2022-04-15:
最后定位到REF板得CAN收发器的一端接触不良有问题导致的，已解决。

Closed 2022-04-15.

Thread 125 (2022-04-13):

关于步进电机力矩反馈

lVRuixiao, 2022-04-13:
请问偶像或则各位大佬：

        步进电机的力反馈是怎么实现的呐，网上还没怎么找到关于步进电机力反馈的资料。
        书上看到的公式是：

                                       T = - (Fδ^2) * Zs * Zr * l * λ * sinθe
                                       Fδ = N * I
        不知道是不是这个也。
感谢感谢！

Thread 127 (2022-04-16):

关于DCE控制疑问

tangul, 2022-04-16:
稚晖君您好，您的驱动程序里位置控制部分使用了“DCE”方法，代码里面的公式好像是这样的
u(k)=kp*ep(k)+∑(ki*ep(m)+kv*ev(m))+kd*ev (k)
看起来和一般串级结构不太一样，像是使用了两个PI控制器求和输出到矢量控制中，而在速度控制中采用了独自的PID控制器。
想知道其中的控制设计原理，谢谢大佬！！

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

peng-zhihui, 2022-04-16:
位置控制还需要考虑到速度的约束，比如希望以某个速度运动到某个位置，所以添加了速度误差和积分，别的操作都是数学上的简化提高运算效率的。

tangul, 2022-04-16:
感谢大佬解答。我仔细看了一下结合梯形加减速的运动规划，确实应该是串级结构。
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

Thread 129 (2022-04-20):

Dummy DLC-AI视觉抓取--手眼标定

19915370507, 2022-04-20:
大佬的视觉抓取定位如此精确，请问大佬的手眼标定方法用的啥子塞

peng-zhihui, 2022-04-20:
OpenCV的solvePNP解算的

19915370507, 2022-04-21:
嗯嗯。请问，您用的是哪种类型的标定板呀 ，  棋盘格还是二维码，还是九点标定的呢。

peng-zhihui, 2022-04-21:
棋盘

19915370507, 2022-04-21:
嗯嗯，谢谢大佬指点。

19915370507, 2022-04-26:
大佬我看您在 Dummy DLC-AI视觉抓取 的视频中说用的是anygrasp ，您是它训练好的模型吗

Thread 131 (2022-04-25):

USB通信

jzijin, 2022-04-25:
稚晖君，你好：
请问下提供的DummyStudio中的USB通信是使用LibUsbDotNet库吗？

jzijin, 2022-04-26:
> 不是，调用底层的C++通信的，用的还是libusb

能否开源USB控制部分的代码呢？

peng-zhihui, 2022-04-26:
开源了啊，仔细看源码和README里面的软件架构图，lowlevel就是。

jzijin, 2022-04-26:
稚晖君，你好。不好意思，我可能没表达清楚，我希望了解的是Dummy Studio.exe上位机中的USB通信部分。REF板中的USB通信部分我知道开源了。

peng-zhihui, 2022-04-26:
那就是串口通信，不涉及USB

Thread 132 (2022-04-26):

关于机器人运动学逆解法的代码细节

LZD0502, 2022-04-26:
1、qs qa qw solFlag是什么意思？

2、R06 与 L6_WRIST 矩阵相乘得到的 L0_wt是啥意思？

3、书中是4x4的位姿矩阵通过左乘Ai^(-1)一步步解耦获得每个角的角度，您的思路是通过把3x3的旋转矩阵与3x1的位置矩阵分开计算的，请问这个算法有没有详细的流程介绍。求稚晖君指点一二。

LZD0502, 2022-04-29:
稚晖君看看我吧 解答下吧 您能告知下您的逆解法的流程是啥嘛？我代码实在看不懂了

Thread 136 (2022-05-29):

刷入固件后，屏幕亮，但是没有出现ref串口号

moai810, 2022-05-29:
刷入2.0固件，端口只有CP2102，没有REF的串口号，救救孩子吧

ZK-y53, 2022-05-29:
枚举出现错误了吧

在 2022-05-29 10:08:39，moai810 ***@***.***> 写道：

刷入2.0固件，端口只有CP2102，没有REF的串口号，救救孩子吧

—
Reply to this email directly, view it on GitHub, or unsubscribe.
You are receiving this because you are subscribed to this thread.Message ID: ***@***.***>

moai810, 2022-05-29:
> 枚举出现错误了吧 在 2022-05-29 10:08:39，moai810 ***@***.***> 写道： 刷入2.0固件，端口只有CP2102，没有REF的串口号，救救孩子吧 — Reply to this email directly, view it on GitHub, or unsubscribe. You are receiving this because you are subscribed to this thread.Message ID: ***@***.***>

大佬可否细讲一下，是代码的问题吗?

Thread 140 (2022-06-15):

求助：42步进电机驱动板问题

mjy2002, 2022-06-15:
板子校准后进入使能状态，但是按键1没有反应，不能失能。芯片是原装STM32F103CBT6,用散新芯片有好用的也有不好用的，用原装芯片就会出现按键1不好使的情况，按键1不好使的情况下CAN通信也就不好使无法控制电机旋转，应该是程序卡再按键循环里面了，不知道怎么解决，希望大家能不忙解决，谢谢

ZXYZZP, 2022-08-15:
>

怎么解决的我也遇到了相同的问题

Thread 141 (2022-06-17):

小朋友学这些，怎么开始，小学毕业，马上初中

sudavida, 2022-06-17:
成长路径怎么样的，谢谢

sudavida, 2022-06-17:
小孩看了你录播的视频，很感兴趣

captain233333, 2022-06-29:
好好做题，考个好高中好大学

zhanglibin102, 2022-07-13:
好好读书，这玩意学还早，上个好高中上个好大学在学都来得及

Mingyang-Li, 2022-07-17:
@sudavida 从小培养学英语的兴趣。把外语学好，走遍天下，学啥都不怕

TanDawn1, 2022-08-14:
先考个好大学

Timoraty, 2022-10-24:
别鸡孩子了，鸡自己把自己鸡个千万身价你孩子下半辈子就可以躺了

ramos-xj7808, 2023-03-17:
sb

xiaocijun, 2023-03-18:
为孩子弄多点钱吧，这玩意超级费钱。弄视频中的那个机械臂起码得1w启动资金

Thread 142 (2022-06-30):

求助：dummystudio连接上ref，拖动模型没有反应，也没有数据上传，有大佬遇到过吗？

SJXCXH, 2022-06-30:

SJXCXH, 2022-06-30:
用CLItool是可以正常通信的

spacomp, 2022-08-14:
我的情况和你的一样，dummystudio连接机械臂没有任何反应，你现在解决了吗？

ZXYZZP, 2022-08-26:
> 用CLItool是可以正常通信的

我的也是studio没法用,请问现在解决了吗

yuZhangNathan, 2022-12-16:
> ol

你好 请问你解决了吗 怎么解决的

bobzuoy, 2023-08-15:
dummystudio 源代码中，好像就没处理这部分，所以无法联动。
感觉OnUsbAsciiCmd函数中需要自己补充完善一下。

zpczpc, 2024-08-07:
> dummystudio 源代码中，好像就没处理这部分，所以无法联动。 感觉OnUsbAsciiCmd函数中需要自己补充完善一下。

你好源码在那个路径下，我没找到

CoderSuHang, 2024-08-07:
您好，我是苏航，感谢您的来信！我会尽快对来信进行查看并尽快给您进行回复，祝您身体健康，工作顺利，谢谢！

zhbi98, 2025-05-10:
Dummy Studio 下发传递的参数是&前缀，源代码中是判断>前缀，所以需要修改下源代码把 > 改为 &，看 dummy_robot.cpp 这个文件。

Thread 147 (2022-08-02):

电机ID参数问题

Joelliamliu, 2022-08-02:
稚晖君您好，修改CMake环境变量后对核心板REF用Clion进行了重新编译，但核心板与主板之间通讯依然有问题，是否需要修改电机ID参数？另外电机的序列号431466563640等是驱动板芯片的序列号还是REF主板J1-J6的跳线号？我刷驱动板程序的时候是否需要修改？还是自动是别的？谢谢！
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

peng-zhihui, 2022-08-02:
序列号和芯片硬件相关，需要自己先读取出来再修改到代码；也可以不管那个序列号，手动一个个电机设置地址就行了，默认都是0地址

Joelliamliu, 2022-08-02:
>

明白了，非常感谢稚晖君不吝赐教！！！

Joelliamliu, 2022-08-05:
> 序列号和芯片硬件相关，需要自己先读取出来再修改到代码；也可以不管那个序列号，手动一个个电机设置地址就行了，默认都是0地址

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

yuZhangNathan, 2022-11-06:
>

请问一下如何获取芯片地址

Zhongliang-liu, 2022-11-07:
下载一个TP-LINK，可以参考https://blog.csdn.net/Zhichao_Zhang/article/details/124411550

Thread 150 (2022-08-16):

电机校准后死机问题

ZXYZZP, 2022-08-16:
hex文件下载进去后，按key1,key2上电，电机开始校准正转两圈反转一圈后停止，停止后按按键没办法使能或者使能电机向是死机了，重新按住按键上电毫无反应无法再进入校准状态.连上stlink utility查看flash发现原本用来储存编码器数据的0x08017C00地址被清空，我想应该是校准失败了但不清楚是什么原因。测试了一下自己编译的固件情况类似不同的是可反复进入校准状态。

ZXYZZP, 2022-08-16:
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

ZXYZZP, 2022-08-17:
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
调试发现程序由于不明错误进入了死循环导致卡死，现在还找不到原因

song-xuyu, 2023-01-09:
你好，请问大佬问题解决了吗？我也出现了这样的问题，就是只要一校准完成(貌似是校准失败)就会进入HardFault_Handler。

KeithBlackmore, 2023-01-10:
可以检查一下编码器使用的磁铁是不是径向充磁的，我更换磁铁后就可以了

Kevin75311, 2023-02-23:
>
请问这个的意思是要在电机底部安装磁铁吗？

song-xuyu, 2023-02-23:
我用clion编译之后flash使用了98%，推测是不是可能cpp编译之后内存太大，校准之后数据存储擦除时将一些段破坏导致进入hardfault，使用xdrive的c版本没有问题

KeithBlackmore, 2023-03-02:
> >
>
> 请问这个的意思是要在电机底部安装磁铁吗？

是的，注意磁铁的物理特性，要径向充磁

Lan-Muzi, 2023-09-15:
> hex文件下载进去后，按key1,key2上电，电机开始校准正转两圈反转一圈后停止，停止后按按键没办法使能或者使能电机向是死机了，重新按住按键上电毫无反应无法再进入校准状态.连上stlink utility查看flash发现原本用来储存编码器数据的0x08017C00地址被清空，我想应该是校准失败了但不清楚是什么原因。测试了一下自己编译的固件情况类似不同的是可反复进入校准状态。

你好，请问这个问题你们如何解决的，我也遇到了这个问题，第一次电机校准的时候是正常的，key1使能/失能闭环都正常，但是后面自己编译了一个固件，改了电机ID，之后就出现这个问题了，能校准，但是校准完之后就不正常了，转动电机有阻尼感，不是完全转不动，但是key1按键完全不起作用，重新上电也是一样 不起作用。同时按住两个按键又可以进行校准，然后就是同样的现象了，换了稚晖君提供的固件也是一样的效果。

Lan-Muzi, 2023-09-15:
> > hex文件下载进去后，按key1,key2上电，电机开始校准正转两圈反转一圈后停止，停止后按按键没办法使能或者使能电机向是死机了，重新按住按键上电毫无反应无法再进入校准状态.连上stlink utility查看flash发现原本用来储存编码器数据的0x08017C00地址被清空，我想应该是校准失败了但不清楚是什么原因。测试了一下自己编译的固件情况类似不同的是可反复进入校准状态。
>
> 你好，请问这个问题你们如何解决的，我也遇到了这个问题，第一次电机校准的时候是正常的，key1使能/失能闭环都正常，但是后面自己编译了一个固件，改了电机ID，之后就出现这个问题了，能校准，但是校准完之后就不正常了，转动电机有阻尼感，不是完全转不动，但是key1按键完全不起作用，重新上电也是一样 不起作用。同时按住两个按键又可以进行校准，然后就是同样的现象了，换了稚晖君提供的固件也是一样的效果。

问题已经解决，原因是掉电重启之后进入错误中断引起，解决方式为在gpio.c文件中注释或者删除相关方法。
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

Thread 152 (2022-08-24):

电机驱动板的丝印问题

raulcao, 2022-08-24:
dbg这个端口的丝印弄反了，GND和DIO，给新入坑的提个醒
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

luhuqiang, 2023-01-05:
所以是gbD才对是吗

luhuqiang, 2023-01-05:
还有什么其他错误吗

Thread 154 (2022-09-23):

志辉先生好，怎么才能直接联系到您，我们有个重要项目想与您合作

wangjianpro999, 2022-09-23:
志辉先生好，怎么才能直接联系到您，我们有个重要项目想与您合作🙏🏻
我们诚恳的希望与您建立更便捷的联系，是否方便回复我们的邮箱wangjianpro@gmail.com，以告知您的电话或微信。方便我们将项目与您沟通，希望一起合作。再次表达我们诚恳的请求🙏🏻

wangjianpro999, 2022-09-23:
也希望贵团队成员看见此信息后转达给志辉先生。我们在焦急的等待中🙏🏻🙏🏻

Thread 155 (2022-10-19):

使用串口发送 p 命令 后，电机停转以后不停抖动大概20°角左右

bigbigbigpick, 2022-10-19:
使用串口发送 p 命令 后，电机停转以后不停抖动大概20°角左右，发送 V 命令 参数为零是可正常停下。 请问下是否是缺省参数问题。如何调整，谢谢。
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

bigbigbigpick, 2022-10-21:
> 确认硬件没问题的话，可能是参数整定的问题，需要自己多尝试几组数据调试下。默认参数是针对42步进电机的。

我是用的电机也是42步进电机，我在这个程序加了这个条语句，它就正常的运行了，造成这个现象可能是什么原因，还有晶振是12MHz 的吗？
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

peng-zhihui, 2022-10-21:
晶振是12MHz。那可能是编译器优化问题，你把release改成debug模式编译看看。

bigbigbigpick, 2022-10-21:
> 晶振是12MHz。那可能是编译器优化问题，你把release改成debug模式编译看看。

遇到了新问题，按照你的要求改成debug 编译时候出现了这种错误 undefined reference to`TB67H450Base::InitGpio()'。
 添加 =0 后 编译出来的代码太大了。达到了121K之多，没办法存放其他数据。会造成单片机死机，在release 模式下没有这个问题
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
编译器版本 应该和你的版本一样吧。能不能解答一下这是什么问题。

peng-zhihui, 2022-10-21:
flash最后要预留32K做校准数据储存区，debug好像是会超过尺寸的，你可以还是换回release模式，然后单独在calcSoftGoal函数前面加上`__attribute__((optimize("O1")))`字段。还是不行的话就需要你自己debug断点调试了，我远程看不出来啥问题。

zucc-zhaob, 2023-01-25:
> > 晶振是12MHz。那可能是编译器优化问题，你把release改成debug模式编译看看。
>
> 遇到了新问题，按照你的要求改成debug 编译时候出现了这种错误 undefined reference to`TB67H450Base::InitGpio()'。 添加 =0 后 编译出来的代码太大了。达到了121K之多，没办法存放其他数据。会造成单片机死机，在release 模式下没有这个问题 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 编译器版本 应该和你的版本一样吧。能不能解答一下这是什么问题。

问题解决了吗？我也遇到这个问题。

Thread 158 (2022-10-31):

调试工具reftool的使用存在问题

zslswlw, 2022-10-31:
连接ref板的usb，运行项目文件夹3.software/cli-tool/run.bat，在终端可以看到“Connected to Dummy-Robot 326133493531 as dummy0”的反馈，但过几秒会显示“Oh no dummy0 disappeared”，终端输入dummy0按tab可以显示提示，下级按tab就没有属性提示了，请问我是哪里没做对吗？
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

zhaoc9527, 2023-09-26:
我也是这个问题，请问解决了没有啊

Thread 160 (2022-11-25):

STM32 Cube IDE 編譯問題 (undefined reference to)

Kevin75311, 2022-11-25:
我使用 Cube IDE 開啟專案後，編譯時發現無法找到 Userapp/common_inc.h
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
將它加入 compiler include 的 PATH 後，變成 common_inc.h 裡面的 function 無法引用 (undefined reference to)
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
想請問是 C 和 C++ 混編造成的問題嗎？ 謝謝！

sytnocui, 2022-11-30:
我把main.cpp的名字改成 userapp.c 就好使了

peng-zhihui, 2022-12-01:
改CMakeLists.txt，不要改path，正常应该是有这个包含路径的，CLion里面clear cache and restart试一下

Closed 2023-07-05.

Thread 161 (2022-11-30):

STM32F4 openocd开发，运行正常，但是debug过不去systemclock-config()函数

sytnocui, 2022-11-30:
稚晖君你好，我最近使用stm32f405rgt6开发项目，使用stlink，clion，openocd调试。发现debug模式无法通过systemclock-config函数，会卡在锁相环初始化这里。只有参考这个网址修改了系统生成的systemclock-config函数才可以正常调试。但是修改系统生成的函数，每次cubemx更新都会覆盖掉，非常不方便，不知道你是怎么解决这个问题的？
我的同学使用stm32cubeide调试，就没有这个问题。
我注意到你在瀚文键盘里的调试器已经改用了cmsis-dap，有没有这方面的考虑？

sytnocui, 2022-11-30:
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
如图所示，会跳进这里，然后卡死

peng-zhihui, 2022-12-01:
main函数最开始加一句RCC_DeInit()就行了，跟DAP没关系，时钟初始化的问题。

sytnocui, 2022-12-01:
> main函数最开始加一句RCC_DeInit()就行了，跟DAP没关系，时钟初始化的问题。

果然可以了，谢谢大佬orz。
另外我也尝试了在stm32cubeide里进行调试，这个调试方式是stlink gdb server，就是什么都不用加就是好使的。我尝试配了一个 clion+gdb+jlink 的debug环境，也是什么都不加就好使。
总结一下就是跟GDB沾边的都是能用的，但用openocd就得加“RCC_DeInit()”这句话。可否再麻烦问一下出现这种情况的详细原因？是和openocd有关系吗？

tip：如果有路人看到了可以参考这篇文章：[CLion配置STM32开发环境（JLink GDB Server）](https://blog.csdn.net/zjh1229/article/details/123887084 )

cmsjscj, 2024-07-07:
感谢万分！！另外我将诸多可能出现的意外情况进行汇总，路人有缘可以去参考下拙作[关于如何使用CLion对于STM32进行调试debug工作的讨论](https://blog.csdn.net/weixin_60664036/article/details/140252907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)

CoderSuHang, 2024-07-07:
您好，我是苏航，感谢您的来信！我会尽快对来信进行查看并尽快给您进行回复，祝您身体健康，工作顺利，谢谢！

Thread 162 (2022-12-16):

关于使用ref-tool发送movel指令时的问题

yuZhangNathan, 2022-12-16:
稚晖君，你好，我调试时遇到以下问题，可以帮我解答一下吗
1、使用ref-tool工具发送movel和movej指令时只输出true，但是机械臂不动，对于每个关节发送set-position指令时可以动，
2、使用上位机时可以连接、但是拖动关节时，机械臂也不动
麻烦了谢谢

yuZhangNathan, 2022-12-16:
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

bobzuoy, 2023-09-19:
我是让 机械臂默认状态下垂，初始状态。

先发送 dummy0.robot.set_enable(1)
然后再发送 dummy0.robot.move_j(-20,-63,100,60,-90,0) 就可以看到机械臂运动了。
复位发送，会返回初始状态。
dummy0.robot.move_j(0,-73,180,0,0,0)

Closed 2023-02-14.

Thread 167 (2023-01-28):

归零的FOC低力矩控制，是否可由位置差来控制

huangwm999, 2023-01-28:
您好，目前的归零和定位设计非常简洁和高效，但FOC的无感模式需要硬件电路上支持，忍不住考虑是否可以移除FOC的无感模式

1. 目前使用了FOC的力矩变大作为归零依据
2. 到达机械零点时绝对值编码器的读取值应该也是有所体现
3. 是否可能以这个做为规律依据
4. 产生位置的相位差异应该等效于力矩变化量

6. 这样FOC的力矩控制可能不是必要的，这样可能可以简化FOC和电路的一些部分
7. 当然 使用FOC的力矩模式，进行动作学习的那个功能也是依赖FOC的力矩模式
8. 但不妨可考虑把静态情况下的位置值变化作为跟随依据

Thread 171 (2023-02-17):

关于闭环驱动 DCE 疑问，DCE 和 PID 是相同的东西 (原理) 吗，谷歌不到 DCE 控制相关的解释

zhbi98, 2023-02-17:
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

正在复刻中，从复刻机械臂核心部件闭环驱动开始，目前正在理解闭环驱动部分代码，已经理解了编码器线性插值校准，电机电流，运行模式，CAN 总线等内容，目前遇到 DCE 的疑问，就是没听过 DCE 这个名词，雉晖君可以简单提示一下吗?

WD-CN73, 2024-04-18:
大佬，想问一下电机电流环的反馈是怎么得到的呢，我看硬件上并没有相关的采样？

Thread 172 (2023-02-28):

大家有没有遇到这个问题，sample 运行显示成功了，但是屏幕不花屏也不显示，抓spi波形发现不对

Jzacky, 2023-02-28:
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
这个波形是刚插上初始化的时候发送的，看着也不大对
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
这个shi'个是运行测试程序，发送的波形，其中黄线是clk 蓝线是数据，感觉数据是发送了，但是发的不对，我抓了两块板子是一样的现象

Closed 2023-02-28.

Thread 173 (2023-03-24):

关于CubeMx生成的工程中，dma初始化在uart初始化之后，造成串口dma传输失败的问题

sytnocui, 2023-03-24:
稚晖君您好，我最近在使用stm32f103c8t6开发的时候，遇到了 cubemx生成的工程uart dma传输失败的问题，经过debug发现是cubemx生成的工程的初始化部分 dma初始化在uart初始化之后，如图，我手动将其调整到uart初始化之前，就好使了。如
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

但是比较郁闷的是，这个问题好像是随机出现的，我的另一个工程就是dma在uart初始化之前，如图
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

请问您遇到过这个问题吗，如果遇到过，是怎么避免的呢，我现在好像只能每次都手操将其位置改变一下，但如果使用cubemx重新生成代码，还要再次手动改变位置

AingSu, 2023-04-07:
cubemax是可以修改初始化顺序的，在project Manager -> Advanced settings 中可以设置

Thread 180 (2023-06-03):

堵转条件检测的疑问

ericQiang, 2023-06-03:
在motor.cpp中，堵转条件的检测代码片段如下：
`if (// Current Mode
            ((controller->modeRunning == MODE_COMMAND_CURRENT ||
              controller->modeRunning == MODE_PWM_CURRENT) &&
             (current != 0))
            || // Other Mode
            current == config.motionParams.ratedCurrent)
        {
            if (abs(controller->estVelocity) < MOTOR_ONE_CIRCLE_SUBDIVIDE_STEPS / 5)
            {
                if (controller->stalledTime >= 1000 * 1000)
                    controller->isStalled = true;
                else
                    controller->stalledTime += motionPlanner.CONTROL_PERIOD;
            }
        } else // can ONLY clear stall flag  MANUALLY
        {
            controller->stalledTime = 0;
        }`
请教，为何在电流模式下的检测条件是：电流不为零，速度小于1/5转持续时间过长。
我理解的是，电流模式就是转出一个恒定的电流（比如恒力矩），此时电机确实是没有转动的，但只要电流（力矩）是我设定的值，那就应该一直这样保持，不应该置位堵转标志。
所以不是很理解这里的电流模式是什么意思。
还望稚晖君给指点迷津。谢谢。

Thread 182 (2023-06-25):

稚晖君你好，我在编译dummy电机驱动的时候报错，请问下是什么原因

haoshuiwuxiang, 2023-06-25:
====================[ Build | Ctrl-Step-STM32-fw.elf | Debug ]==================
"C:\Program Files\JetBrains\CLion 2021.2.2\bin\cmake\win\bin\cmake.exe" --build D:\STM32\Dummy-Robot-main\2.Firmware\Ctrl-Step-Driver-STM32F1-fw\cmake-build-debug --target Ctrl-Step-STM32-fw.elf -- -j 19
[  1%] Linking CXX executable Ctrl-Step-STM32-fw.elf
d:/stm32/clion_stm32_windows/gcc-arm-none-eabi/bin/../lib/gcc/arm-none-eabi/10.3.1/../../../../arm-none-eabi/bin/ld.exe: CMakeFiles/Ctrl-Step-STM32-fw.elf.dir/Ctrl/Driver/tb67h450_base.cpp.obj:(.rodata._ZTV12TB67H450Base+0x1c): undefined reference to `TB67H450Base::InitGpio()'
d:/stm32/clion_stm32_windows/gcc-arm-none-eabi/bin/../lib/gcc/arm-none-eabi/10.3.1/../../../../arm-none-eabi/bin/ld.exe: CMakeFiles/Ctrl-Step-STM32-fw.elf.dir/Ctrl/Driver/tb67h450_base.cpp.obj:(.rodata._ZTV12TB67H450Base+0x20): undefined reference to `TB67H450Base::InitPwm()'
d:/stm32/clion_stm32_windows/gcc-arm-none-eabi/bin/../lib/gcc/arm-none-eabi/10.3.1/../../../../arm-none-eabi/bin/ld.exe: CMakeFiles/Ctrl-Step-STM32-fw.elf.dir/Ctrl/Driver/tb67h450_base.cpp.obj:(.rodata._ZTV12TB67H450Base+0x24): undefined reference to `TB67H450Base::DacOutputVoltage(unsigned short, unsigned short)'
d:/stm32/clion_stm32_windows/gcc-arm-none-eabi/bin/../lib/gcc/arm-none-eabi/10.3.1/../../../../arm-none-eabi/bin/ld.exe: CMakeFiles/Ctrl-Step-STM32-fw.elf.dir/Ctrl/Driver/tb67h450_base.cpp.obj:(.rodata._ZTV12TB67H450Base+0x28): undefined reference to `TB67H450Base::SetInputA(bool, bool)'
d:/stm32/clion_stm32_windows/gcc-arm-none-eabi/bin/../lib/gcc/arm-none-eabi/10.3.1/../../../../arm-none-eabi/bin/ld.exe: CMakeFiles/Ctrl-Step-STM32-fw.elf.dir/Ctrl/Driver/tb67h450_base.cpp.obj:(.rodata._ZTV12TB67H450Base+0x2c): undefined reference to `TB67H450Base::SetInputB(bool, bool)'
d:/stm32/clion_stm32_windows/gcc-arm-none-eabi/bin/../lib/gcc/arm-none-eabi/10.3.1/../../../../arm-none-eabi/bin/ld.exe: CMakeFiles/Ctrl-Step-STM32-fw.elf.dir/Ctrl/Sensor/Encoder/mt6816_base.cpp.obj:(.rodata._ZTV10MT6816Base+0x14): undefined reference to `MT6816Base::SpiInit()'
d:/stm32/clion_stm32_windows/gcc-arm-none-eabi/bin/../lib/gcc/arm-none-eabi/10.3.1/../../../../arm-none-eabi/bin/ld.exe: CMakeFiles/Ctrl-Step-STM32-fw.elf.dir/Ctrl/Sensor/Encoder/mt6816_base.cpp.obj:(.rodata._ZTV10MT6816Base+0x18): undefined reference to `MT6816Base::SpiTransmitAndRead16Bits(unsigned short)'
collect2.exe: error: ld returned 1 exit status
mingw32-make.exe[3]: *** [CMakeFiles\Ctrl-Step-STM32-fw.elf.dir\build.make:827: Ctrl-Step-STM32-fw.elf] Error 1
mingw32-make.exe[2]: *** [CMakeFiles\Makefile2:82: CMakeFiles/Ctrl-Step-STM32-fw.elf.dir/all] Error 2
mingw32-make.exe[1]: *** [CMakeFiles\Makefile2:89: CMakeFiles/Ctrl-Step-STM32-fw.elf.dir/rule] Error 2
mingw32-make.exe: *** [Makefile:123: Ctrl-Step-STM32-fw.elf] Error 2

MarPotato, 2023-07-12:
我也遇到了相同的问题，困扰我一周了，看网上说是没有include相应的头文件，我试了一下，但错误更多了，不知道老哥解决了吗？

MarPotato, 2023-07-13:
老哥，问题解决了，有小伙伴询问过智晖君，解决办法是：更换gcc-arm-none-eabi版本为9.2.1

MarPotato, 2023-07-14:
> 重新配置运行环境 在 2023-06-25 09:39:59，haoshuiwuxiang ***@***.***> 写道： ====================[ Build | Ctrl-Step-STM32-fw.elf | Debug ]================== "C:\Program Files\JetBrains\CLion 2021.2.2\bin\cmake\win\bin\cmake.exe" --build D:\STM32\Dummy-Robot-main\2.Firmware\Ctrl-Step-Driver-STM32F1-fw\cmake-build-debug --target Ctrl-Step-STM32-fw.elf -- -j 19 [ 1%] Linking CXX executable Ctrl-Step-STM32-fw.elf d:/stm32/clion_stm32_windows/gcc-arm-none-eabi/bin/../lib/gcc/arm-none-eabi/10.3.1/../../../../arm-none-eabi/bin/ld.exe: CMakeFiles/Ctrl-Step-STM32-fw.elf.dir/Ctrl/Driver/tb67h450_base.cpp.obj:(.rodata._ZTV12TB67H450Base+0x1c): undefined reference to TB67H450Base::InitGpio()' d:/stm32/clion_stm32_windows/gcc-arm-none-eabi/bin/../lib/gcc/arm-none-eabi/10.3.1/../../../../arm-none-eabi/bin/ld.exe: CMakeFiles/Ctrl-Step-STM32-fw.elf.dir/Ctrl/Driver/tb67h450_base.cpp.obj:(.rodata._ZTV12TB67H450Base+0x20): undefined reference to TB67H450Base::InitPwm()' d:/stm32/clion_stm32_windows/gcc-arm-none-eabi/bin/../lib/gcc/arm-none-eabi/10.3.1/../../../../arm-none-eabi/bin/ld.exe: CMakeFiles/Ctrl-Step-STM32-fw.elf.dir/Ctrl/Driver/tb67h450_base.cpp.obj:(.rodata._ZTV12TB67H450Base+0x24): undefined reference to TB67H450Base::DacOutputVoltage(unsigned short, unsigned short)' d:/stm32/clion_stm32_windows/gcc-arm-none-eabi/bin/../lib/gcc/arm-none-eabi/10.3.1/../../../../arm-none-eabi/bin/ld.exe: CMakeFiles/Ctrl-Step-STM32-fw.elf.dir/Ctrl/Driver/tb67h450_base.cpp.obj:(.rodata._ZTV12TB67H450Base+0x28): undefined reference to TB67H450Base::SetInputA(bool, bool)' d:/stm32/clion_stm32_windows/gcc-arm-none-eabi/bin/../lib/gcc/arm-none-eabi/10.3.1/../../../../arm-none-eabi/bin/ld.exe: CMakeFiles/Ctrl-Step-STM32-fw.elf.dir/Ctrl/Driver/tb67h450_base.cpp.obj:(.rodata._ZTV12TB67H450Base+0x2c): undefined reference to TB67H450Base::SetInputB(bool, bool)' d:/stm32/clion_stm32_windows/gcc-arm-none-eabi/bin/../lib/gcc/arm-none-eabi/10.3.1/../../../../arm-none-eabi/bin/ld.exe: CMakeFiles/Ctrl-Step-STM32-fw.elf.dir/Ctrl/Sensor/Encoder/mt6816_base.cpp.obj:(.rodata._ZTV10MT6816Base+0x14): undefined reference to MT6816Base::SpiInit()' d:/stm32/clion_stm32_windows/gcc-arm-none-eabi/bin/../lib/gcc/arm-none-eabi/10.3.1/../../../../arm-none-eabi/bin/ld.exe: CMakeFiles/Ctrl-Step-STM32-fw.elf.dir/Ctrl/Sensor/Encoder/mt6816_base.cpp.obj:(.rodata._ZTV10MT6816Base+0x18): undefined reference to `MT6816Base::SpiTransmitAndRead16Bits(unsigned short)' collect2.exe: error: ld returned 1 exit status mingw32-make.exe[3]: *** [CMakeFiles\Ctrl-Step-STM32-fw.elf.dir\build.make:827: Ctrl-Step-STM32-fw.elf] Error 1 mingw32-make.exe[2]: *** [CMakeFiles\Makefile2:82: CMakeFiles/Ctrl-Step-STM32-fw.elf.dir/all] Error 2 mingw32-make.exe[1]: *** [CMakeFiles\Makefile2:89: CMakeFiles/Ctrl-Step-STM32-fw.elf.dir/rule] Error 2 mingw32-make.exe: *** [Makefile:123: Ctrl-Step-STM32-fw.elf] Error 2 — Reply to this email directly, view it on GitHub, or unsubscribe. You are receiving this because you are subscribed to this thread.Message ID: ***@***.***>

更换gcc-arm-none-eabi版本为9.2.1

MarPotato, 2023-07-14:
更换gcc-arm-none-eabi版本为9.2.1

---- 回复的原邮件 ----
| 发件人 | ***@***.***> |
| 日期 | 2023年07月14日 18:00 |
| 收件人 | ***@***.***> |
| 抄送至 | ***@***.***>***@***.***> |
| 主题 | Re: [peng-zhihui/Dummy-Robot] 稚晖君你好，我在编译dummy电机驱动的时候报错，请问下是什么原因 (Issue #182) |

重新配置运行环境

在 2023-06-25 09:39:59，haoshuiwuxiang ***@***.***> 写道：

====================[ Build | Ctrl-Step-STM32-fw.elf | Debug ]==================
"C:\Program Files\JetBrains\CLion 2021.2.2\bin\cmake\win\bin\cmake.exe" --build D:\STM32\Dummy-Robot-main\2.Firmware\Ctrl-Step-Driver-STM32F1-fw\cmake-build-debug --target Ctrl-Step-STM32-fw.elf -- -j 19
[ 1%] Linking CXX executable Ctrl-Step-STM32-fw.elf
d:/stm32/clion_stm32_windows/gcc-arm-none-eabi/bin/../lib/gcc/arm-none-eabi/10.3.1/../../../../arm-none-eabi/bin/ld.exe: CMakeFiles/Ctrl-Step-STM32-fw.elf.dir/Ctrl/Driver/tb67h450_base.cpp.obj:(.rodata._ZTV12TB67H450Base+0x1c): undefined reference to TB67H450Base::InitGpio()' d:/stm32/clion_stm32_windows/gcc-arm-none-eabi/bin/../lib/gcc/arm-none-eabi/10.3.1/../../../../arm-none-eabi/bin/ld.exe: CMakeFiles/Ctrl-Step-STM32-fw.elf.dir/Ctrl/Driver/tb67h450_base.cpp.obj:(.rodata._ZTV12TB67H450Base+0x20): undefined reference to TB67H450Base::InitPwm()'
d:/stm32/clion_stm32_windows/gcc-arm-none-eabi/bin/../lib/gcc/arm-none-eabi/10.3.1/../../../../arm-none-eabi/bin/ld.exe: CMakeFiles/Ctrl-Step-STM32-fw.elf.dir/Ctrl/Driver/tb67h450_base.cpp.obj:(.rodata._ZTV12TB67H450Base+0x24): undefined reference to TB67H450Base::DacOutputVoltage(unsigned short, unsigned short)' d:/stm32/clion_stm32_windows/gcc-arm-none-eabi/bin/../lib/gcc/arm-none-eabi/10.3.1/../../../../arm-none-eabi/bin/ld.exe: CMakeFiles/Ctrl-Step-STM32-fw.elf.dir/Ctrl/Driver/tb67h450_base.cpp.obj:(.rodata._ZTV12TB67H450Base+0x28): undefined reference to TB67H450Base::SetInputA(bool, bool)'
d:/stm32/clion_stm32_windows/gcc-arm-none-eabi/bin/../lib/gcc/arm-none-eabi/10.3.1/../../../../arm-none-eabi/bin/ld.exe: CMakeFiles/Ctrl-Step-STM32-fw.elf.dir/Ctrl/Driver/tb67h450_base.cpp.obj:(.rodata._ZTV12TB67H450Base+0x2c): undefined reference to TB67H450Base::SetInputB(bool, bool)' d:/stm32/clion_stm32_windows/gcc-arm-none-eabi/bin/../lib/gcc/arm-none-eabi/10.3.1/../../../../arm-none-eabi/bin/ld.exe: CMakeFiles/Ctrl-Step-STM32-fw.elf.dir/Ctrl/Sensor/Encoder/mt6816_base.cpp.obj:(.rodata._ZTV10MT6816Base+0x14): undefined reference to MT6816Base::SpiInit()'
d:/stm32/clion_stm32_windows/gcc-arm-none-eabi/bin/../lib/gcc/arm-none-eabi/10.3.1/../../../../arm-none-eabi/bin/ld.exe: CMakeFiles/Ctrl-Step-STM32-fw.elf.dir/Ctrl/Sensor/Encoder/mt6816_base.cpp.obj:(.rodata._ZTV10MT6816Base+0x18): undefined reference to `MT6816Base::SpiTransmitAndRead16Bits(unsigned short)'
collect2.exe: error: ld returned 1 exit status
mingw32-make.exe[3]: *** [CMakeFiles\Ctrl-Step-STM32-fw.elf.dir\build.make:827: Ctrl-Step-STM32-fw.elf] Error 1
mingw32-make.exe[2]: *** [CMakeFiles\Makefile2:82: CMakeFiles/Ctrl-Step-STM32-fw.elf.dir/all] Error 2
mingw32-make.exe[1]: *** [CMakeFiles\Makefile2:89: CMakeFiles/Ctrl-Step-STM32-fw.elf.dir/rule] Error 2
mingw32-make.exe: *** [Makefile:123: Ctrl-Step-STM32-fw.elf] Error 2

—
Reply to this email directly, view it on GitHub, or unsubscribe.
You are receiving this because you are subscribed to this thread.Message ID: ***@***.***>

—
Reply to this email directly, view it on GitHub, or unsubscribe.
You are receiving this because you commented.Message ID: ***@***.***>

lixinswitchpi, 2023-07-17:
试试编译release模式

Tundon, 2023-08-09:
> 老哥，问题解决了，有小伙伴询问过智晖君，解决办法是：更换gcc-arm-none-eabi版本为9.2.1

或者用新版gcc-arm，手动加入那几个虚函数的空实现`virtual xxx() {}`。不过新版gcc-arm编译出来的文件大了，就没有足够空间给校验数据了。所以还是推荐换gcc-arm到9.2.1

mzrjfft, 2024-08-18:
我的烧录进去之后依旧挺大
Memory region         Used Size  Region Size  %age Used
             RAM:        7696 B        20 KB     37.58%
           FLASH:      114640 B       128 KB     87.46%
而且烧录进去之后无法点亮ref屏了

mzrjfft, 2024-08-18:
有什么可以修改flash大小吗

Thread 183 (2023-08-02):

继续蹲Dummy青春版

Jeck-Liu-Create, 2023-08-02:
不知道还有没有希望，稚晖君创业如何了

lixiyu, 2023-10-10:
+1, 今天刷到一个国外 1W 美元硬件成本的机械臂。
看来看去，还是稚晖君的好。
等保姆级教程出来我也冲。

jli113, 2023-11-20:
Still waiting

CoderSuHang, 2023-11-20:
您好，我是苏航，感谢您的来信！我会尽快对来信进行查看并尽快给您进行回复，祝您身体健康，工作顺利，谢谢！

xxxwenjie, 2024-09-30:
蹲

CoderSuHang, 2024-09-30:
您好，我是苏航，感谢您的来信！我会尽快对来信进行查看并尽快给您进行回复，祝您身体健康，工作顺利，谢谢！

san-holy, 2024-11-28:
蹲

gujiaofadianchamg, 2025-03-18:
接着蹲

CoderSuHang, 2025-03-18:
您好，我是苏航，感谢您的来信！我会尽快对来信进行查看并尽快给您进行回复，祝您身体健康，工作顺利，谢谢！

CoderSuHang, 2025-07-22:
您好，我是苏航，感谢您的来信！我会尽快对来信进行查看并尽快给您进行回复，祝您身体健康，工作顺利，谢谢！

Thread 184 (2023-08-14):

解决42固件最新arm gcc 编译文件过大无法存放校准数据问题

lixinswitchpi, 2023-08-14:
用最新的arm-none-eabi-gcc(12.2.1 20230214)编译42固件过大120k，会覆盖校准数据，问题出在interface_uart.cpp sscanf函数在新版中会占用50k的空间，用strtok atof替换后，固件只占79k，满足最大0x08017C00-1的要求
 FLASH:       78932 B       128 KB     60.22%

可以直接用下面代码覆盖原先的interface_uart.cpp，用clion重新编译即可

#include "common_inc.h"
#include "configurations.h"
#include <string.h>
#include <stdlib.h>

extern Motor motor;

void OnUartCmd(uint8_t* _data, uint16_t _len)
{
    float cur, pos, vel, time;
    char *token = NULL;
    switch (_data[0])
    {
        case 'c':
            token = strtok((char*) _data, "c");
            cur = atof(token);
            if (motor.controller->modeRunning != Motor::MODE_COMMAND_CURRENT)
                motor.controller->SetCtrlMode(Motor::MODE_COMMAND_CURRENT);
            motor.controller->SetCurrentSetPoint((int32_t) (cur * 1000));
            break;
        case 'v':
            token = strtok((char*) _data, "v");
            vel = atof(token);
            if (motor.controller->modeRunning != Motor::MODE_COMMAND_VELOCITY)
            {
                motor.config.motionParams.ratedVelocity = boardConfig.velocityLimit;
                motor.controller->SetCtrlMode(Motor::MODE_COMMAND_VELOCITY);
            }
            motor.controller->SetVelocitySetPoint(
                (int32_t) (vel * (float) motor.MOTOR_ONE_CIRCLE_SUBDIVIDE_STEPS));
            break;
        case 'p':
            token = strtok((char*) _data, "p");
            pos = atof(token);
            if (motor.controller->modeRunning != Motor::MODE_COMMAND_POSITION)
                motor.controller->requestMode = Motor::MODE_COMMAND_POSITION;

            motor.controller->SetPositionSetPoint(
                (int32_t) (pos * (float) motor.MOTOR_ONE_CIRCLE_SUBDIVIDE_STEPS));
            break;
        default:
            printf("Only support [c] [v] [p] commands!\r\n");
            break;
    }
}

bobzuoy, 2023-08-15:
用的 gcc-arm-none-eabi-9-2019-q4-major-win32 ，还好能编译过。

Yuz1i, 2023-09-14:
你好，我想问一下，为什么我将OnUartCmd里面的内容都注释后编译还是80%的占用呢？

lixinswitchpi, 2023-09-15:
发代码上来看看？另外，你直接用我的虚拟机环境试试 https://www.bilibili.com/video/BV1Bm4y1K7fY

Yuz1i, 2023-09-15:
> 发代码上来看看？另外，你直接用我的虚拟机环境试试 https://www.bilibili.com/video/BV1Bm4y1K7fY

好的好的，谢谢你。我的代码就是现在仓库的代码，然后将OnUartCmd函数注释。但是我是在windows环境下交叉编译的，然后我试一下你的虚拟机吧，万分感谢！！！

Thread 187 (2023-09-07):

打开即用Dummy固件编译/debug/下载虚拟机

lixinswitchpi, 2023-09-07:
肝了一晚，配置了一个dummy固件编译和debug环境的vbox的虚拟机，方便对软件不熟悉的小伙伴打开即用！直接编译，插上st-link（v2）即可debug和下载，环境包括
1 Clion23.2(已经解除限制，但只限个人学习使用，商业应用后果自负)
2 最新版ARM toolchain 12.3.rel1-x86_64-arm-none-eabi
3 OpenOCD，已经配置到两个项目中，可以直接debug并下载到板子
4 最新stm32 programmer
5 Ubuntu22.04.2 LTS

修复了几个最新toolchain下的bug
1 42固件编译后过大，占用校验数据bug
2 支持Dummy studio的命令格式
3 42固件 ST-LINK 配置错误
4 fixed undefined reference to `TB67H450Base::InitGpio()' ... 等等 issues
5 fixed error: there are no arguments to 'snprintf' that depend on a template parameter, so a declaration of 'snprintf' must be available [␛]8;;https://gcc.gnu.org/onlinedocs/gcc/Warning-Options.html#index-fpermissive␇-fpermissive␛]8;;␇]
6 fixed error: 'string' in namespace 'std' does not name a type
7 fixed fatal error: mpu6050.hpp: No such file or directory
.....
另外，为了方便大家上手，制作了一个简单视频供参考（刚发现录制时没开mic，没有声音 :( 最近有点儿忙，过两天补上 :)

References:
虚拟机
https://pan.baidu.com/s/1hgVCwm78P3Q80ixG1-m_Hg 提取码：dqgx
视频
https://www.bilibili.com/video/BV1Bm4y1K7fY/
VM VirtualBOX
https://www.virtualbox.org/wiki/Downloads
ARM GNU Toolchain
https://developer.arm.com/downloads/-/gnu-rm
Dummy GitHub
https://github.com/peng-zhihui/Dummy-Robot
OpenOCD
https://openocd.org/

Gabriel1688, 2024-01-26:
上面的虚拟机链接过期了， 能再发一次吗？谢谢

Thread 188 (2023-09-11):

CAN Bus 傳輸問題

Kevin75311, 2023-09-11:
稚暉君您好，
目前可以用 USB 和 REF 板子溝通，但無法透過 ref_tool CAN 跟馬達板溝通 (目前只連接 ID=1 的馬達)，
1. 有檢查過 CAN1, CAN2 initialize 都正常，馬達連接 CAN1
2. 測試連接一個馬達，終端電阻有焊接，CAN BUS 上電阻為 60 ohms
3. 無操作時 CAN_H 電壓 2.23V，CAN_L 電壓 2.20V

想請問一下，目前可以量測到發出的訊號如下：
* joint_1.do_calibration()
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
* joint_1.update_angle()
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
但是馬達沒有任何反應，想請問可能是什麼問題呢？

CAN Bus 上會一直出現固定的訊號如下，不確定是不是正常的：
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

非常感謝~

lixinswitchpi, 2023-09-12:
参考一下下面的视频关于REF与Motor CAN BUS 通信例程，尝试debug motor 1 端的CAN BUS接收数据，看看能不能发现问题。另外，CAN BUS的两条线是双绞线，并行的话会出现此类问题。
https://www.bilibili.com/video/BV1E34y1K7KZ/

Kevin75311, 2023-09-13:
您好，非常感謝您，您的影片非常有幫助。
有一些電路接線的細節，想請問我理解有沒有錯誤：
1.如果接1個馬達，這樣一個 120-ohm 的電阻在電機電路板上，另外一個終端電阻要在自行焊接 (因為REF板上沒有電阻)？
2.如果接6個馬達，這樣在頭尾的電機電路板焊接120 ohm的電阻即可，其餘中間的電機電路板皆不必焊接電阻？
中間的連線接用雙絞線連接。

非常感謝您~

lixinswitchpi, 2023-09-13:
1. 是的，motor端需要接上终端电阻，稚晖君的ref上有设计终端电阻，这个需要始终enable
2. 对，CAN总线的两端都需要接120欧姆终端电阻,以匹配总线特性阻抗,保证信号质量。中间motor不需要接
我有一个改版的motor驱动板最近会发布，加上了一个switch，可以方便的打开或关闭120欧姆终端电阻，另外pcb重新布局，布线，优化了模拟信号，gnd，电源gnd等等，你可以关注我的b站

Closed 2023-10-05.

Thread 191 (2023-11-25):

DummyStudio的命令与源代码不一致

bobzuoy, 2023-11-25:
发现传递的参数是&，源代码中是> ,所以不联动。
这里需要修改下源代码中的文件。就可以联动了。

https://github.com/peng-zhihui/Dummy-Robot/assets/142277489/decf0559-78f8-4b65-bd11-77090820b139

lkz-2000, 2023-12-07:
您好，请问一下这个软件能实现离线编程吗，就是输入轨迹，生成各个关节角运动

bobzuoy, 2023-12-07:
可以的。适当修CLI-Tool，应该就可以了。
可以外面放一个树莓派来实现更多功能。我改了一个python flask的网页控制。
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

zhbi98, 2025-05-09:
同样遇到这个问题

zhbi98, 2025-05-09:
> 发现传递的参数是&，源代码中是> ,所以不联动。 这里需要修改下源代码中的文件。就可以联动了。
> 489a2984be3a685447394f80f6845620.mp4

> 发现传递的参数是&，源代码中是> ,所以不联动。 这里需要修改下源代码中的文件。就可以联动了。
> 489a2984be3a685447394f80f6845620.mp4

没错，我同样遇到这个问题，一度怀疑是丢失了 & 字段标识的数据解析，或是在 > 标识中包含了这段解析

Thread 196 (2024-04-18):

请教一下大佬，关于FOC电流环控制

WD-CN73, 2024-04-18:
我看控制板的PCB中没有对电流采样，那么在软件里是怎么实现电流环的控制的呢，getfoccurrent的值是怎么来的呢？

hhlyyy, 2024-05-10:
同问！

hhlyyy, 2024-05-10:
困扰好久了

CoderSuHang, 2024-05-10:
您好，我是苏航，感谢您的来信！我会尽快对来信进行查看并尽快给您进行回复，祝您身体健康，工作顺利，谢谢！

WD-CN73, 2024-05-15:
> 困扰好久了

最近了解了其实是用高频斩波恒流来操作，可以看一下那个电机驱动芯片里的pwm恒流控制。

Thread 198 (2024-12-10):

运动学移植的问题

Zz-er, 2024-12-10:
运动学部分似乎有一些问题，我在迁移到别的机械臂上时，就正向运动学接口来说，如下图所示首先构造Dof6Kinematic类，并且确保L_BS, D_BS, L_AM, L_FA, D_EW, L_WT的单位是m，
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
下面是我对正向运动学接口做的封装，确保输入的角度单位是度，转化输出的pose将xyz单位从m转换为mm，并将输出的欧拉角单位从度转换为弧度
```

Eigen::Matrix4d pzh_KinematicsSolverAdapter::fk(const std::vector<double>& joints, int* errType)
{
	assert(joints.size() == 6);
	assert(_dhParams.size() >= 6);
	DOF6Kinematic::Joint6D_t joint_t;

	for (int i = 0; i < 6; i++)
	{
		joint_t.a[i] = (joints[i] + _dhParams[i].theta) * MathUtil::RAD2DEG;
	}

	DOF6Kinematic::Pose6D_t pose_t;

	bool flag = _kin->SolveFK(joint_t, pose_t);
	if (flag)
	{
		if (errType)
			*errType = Fk_NoError;

		Eigen::Matrix4d matrix = Eigen::Matrix4d::Identity();
		matrix.block<3, 1>(0, 3) = Eigen::Vector3d(pose_t.X*1000, pose_t.Y*1000,  pose_t.Z*1000);
		matrix.block<3, 3>(0, 0) = MathUtil::eulerAnglesToMatrix3d(Eigen::Vector3d(pose_t.A*MathUtil::DEG2RAD, pose_t.B * MathUtil::DEG2RAD, pose_t.C * MathUtil::DEG2RAD), MathUtil::EulerOrder::ZYX);
		return matrix;
	}
	else
	{
		if (errType)
			*errType = Fk_Error;

		return Eigen::Matrix4d::Identity();
	}
}
```
得到的位姿显示在场景中如图所示
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
我自认为已经做了比较详尽的检查了，请问我还有哪里没有检查到吗？但是无法适用，我所做的检查主要是
1. 构造函数 DOF6Kinematic(float L_BS, float D_BS, float L_AM, float L_FA, float D_EW, float L_WT)，确定参数的单位和数值
2. 正向运动学接口 bool DOF6Kinematic::SolveFK(const DOF6Kinematic::Joint6D_t& _inputJoint6D, DOF6Kinematic::Pose6D_t& _outputPose6D)，确定关节角单位为角度，转换输出位姿的单位，我已经从m转换成mm了，欧拉角也从角度转换成了我使用的弧度

============================
此外还发现代码中一个SDH表定义的构型似乎有问题，但是对后面的计算并没有影响，后面的计算中并没有访问dh表中的d和a参数
如下图所示6dof_kinematics.cpp文件中tmp_DH_matrix定义的SDH构型
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
将上面的构型用matlab绘制出来如下图所示
`
% 清除环境
clear all; close all; clc;

% 注意：Link的参数顺序为 [theta d a alpha]
L1 = Link([0        0.550  0.180  -pi/2]);
L2 = Link([-pi/2    0    0.680   0   ]);
L3 = Link([pi/2        0.165    0  pi/2]);
% L3 = Link([pi/2        0    -0.165  pi/2]); % L3的DH参数应该定义成这样
L4 = Link([0         0.842  0    -pi/2]);
L5 = Link([0         0    0    pi/2]);
L6 = Link([0         0.12    0    0   ]);
% 创建机器人模型，将所有链节按顺序组合
SDH_robot = SerialLink([L1 L2 L3 L4 L5 L6], 'name', 'SDHRobot');
view(3)

% SDH_robot.plot([0 0 0 0 0 0]);

% 设置机器人绘图参数（可选）
SDH_robot.display

SDH_robot.teach([0 -pi/2 pi/2 0 0 0]);`
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
D_ELBOW参数和示意图中描述的不同
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
启用上面matlab代码中的注释，将L3定义为 L3 = Link([pi/2        0    -0.165  pi/2]);
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
虽然对后面的计算没有影响，应该定义为
```
    float tmp_DH_matrix[6][4] = {
        // theta            d                   a                   alpha
        {0.0f,            armConfig.L_BASE,    armConfig.D_BASE, -(float)M_PI_2},
        {-(float)M_PI_2, 0.0f,                armConfig.L_ARM,  0.0f},
        {(float)M_PI_2,  0.0f,                 -armConfig.D_ELBOW, (float)M_PI_2},
        {0.0f,            armConfig.L_FOREARM, 0.0f,             -(float)M_PI_2},
        {0.0f,            0.0f,                0.0f,             (float)M_PI_2},
        {0.0f,            armConfig.L_WRIST, 0.0f, 0.0f}
    };
```
3.

linqingjue, 2025-07-24:
3关节图示状态是90°状态，并且根据上位机来看规定的正向旋转判断Z轴，我得出来的旋转矩阵`float tmp_DH_matrix[6][4] = {
        {0.0f,            armConfig.L_BASE,    armConfig.D_BASE, -(float) M_PI_2},
        {-(float) M_PI_2, 0.0f,                armConfig.L_ARM,  0.0f},
        {0,               0.0f,                armConfig.D_ELBOW, (float) M_PI_2},
        {0.0f,            armConfig.L_FOREARM, 0.0f,             (float) M_PI_2},
        {0.0f,            0.0f,                0.0f,             -(float) M_PI_2},
        {0.0f,            armConfig.L_WRIST,   0.0f,             0.0f}
    };`

linqingjue, 2025-07-24:
例图里关节3是90°状态，我根据上位机角度旋转方向判断的Z轴朝向，最后得到的矩阵是这个：
```
float tmp_DH_matrix[6][4] = {
        {0.0f,            armConfig.L_BASE,    armConfig.D_BASE, -(float) M_PI_2},
        {-(float) M_PI_2, 0.0f,                armConfig.L_ARM,  0.0f},
        {0,               0.0f,                armConfig.D_ELBOW, (float) M_PI_2},
        {0.0f,            armConfig.L_FOREARM, 0.0f,             (float) M_PI_2},
        {0.0f,            0.0f,                0.0f,             -(float) M_PI_2},
        {0.0f,            armConfig.L_WRIST,   0.0f,             0.0f}
    };
```

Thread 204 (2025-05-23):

Dummy 零点 HomeOffset 校准问题？

zhbi98, 2025-05-23:
为什么 Dummy 要设置两次零点？第一次是 L 形的时候设置一下，复位姿势后在设置一下。在机械臂回到休息姿势（Resting Pose）后再应用一次“当前位置作为零点”（ApplyPositionAsHome），那么最后零点不就会以休息姿势来定义？

<!-- Failed to upload "7250298F618EEEBF6EC78C274B192324.png" -->

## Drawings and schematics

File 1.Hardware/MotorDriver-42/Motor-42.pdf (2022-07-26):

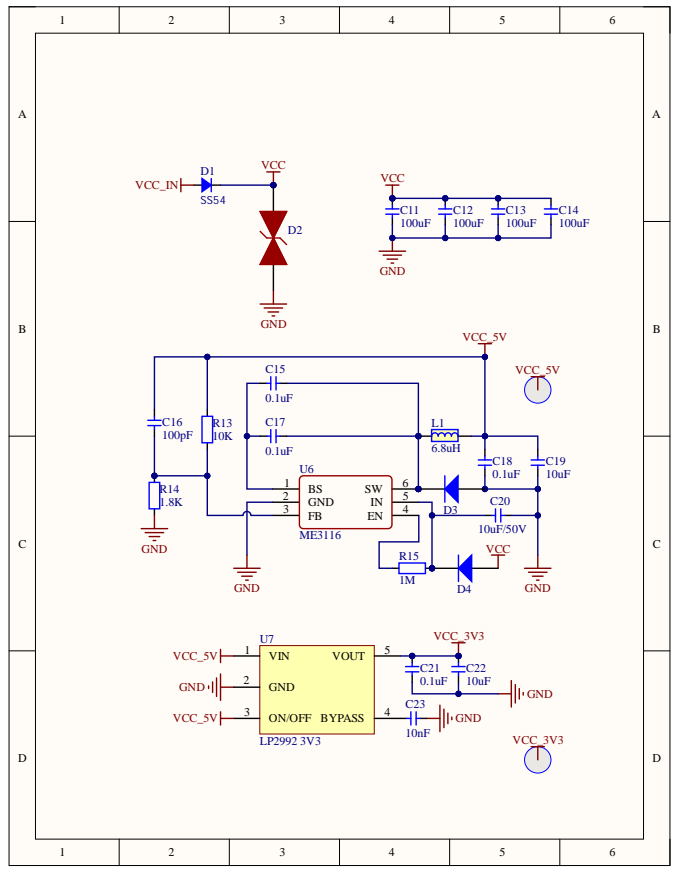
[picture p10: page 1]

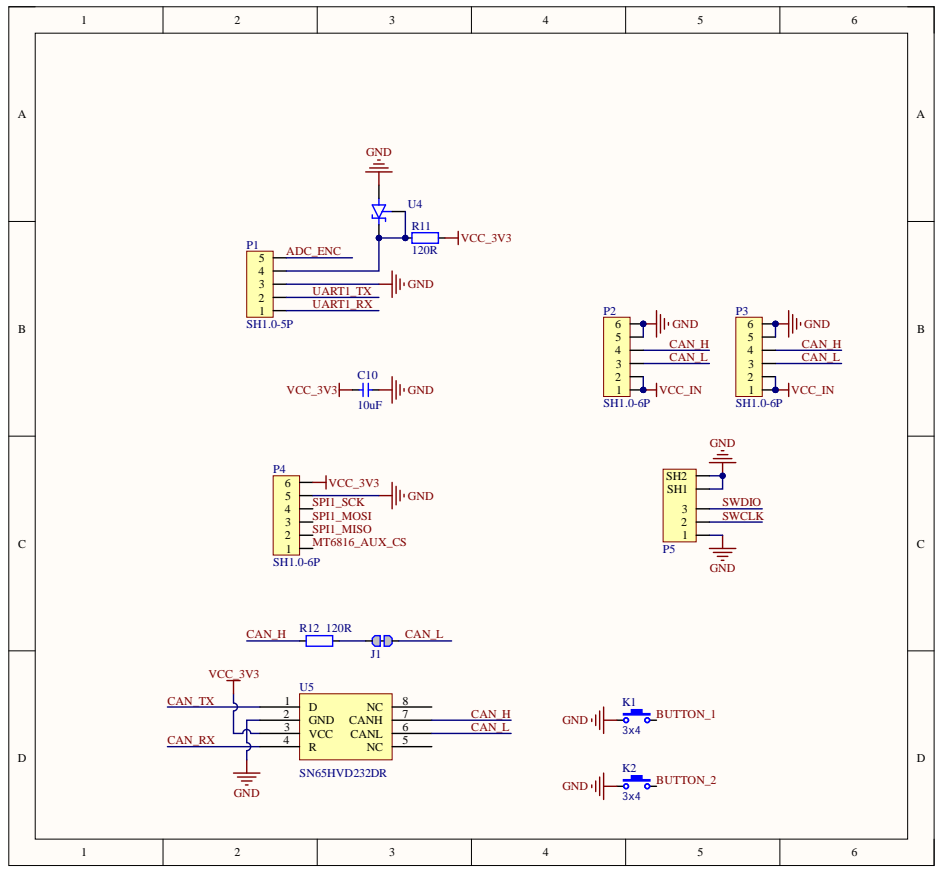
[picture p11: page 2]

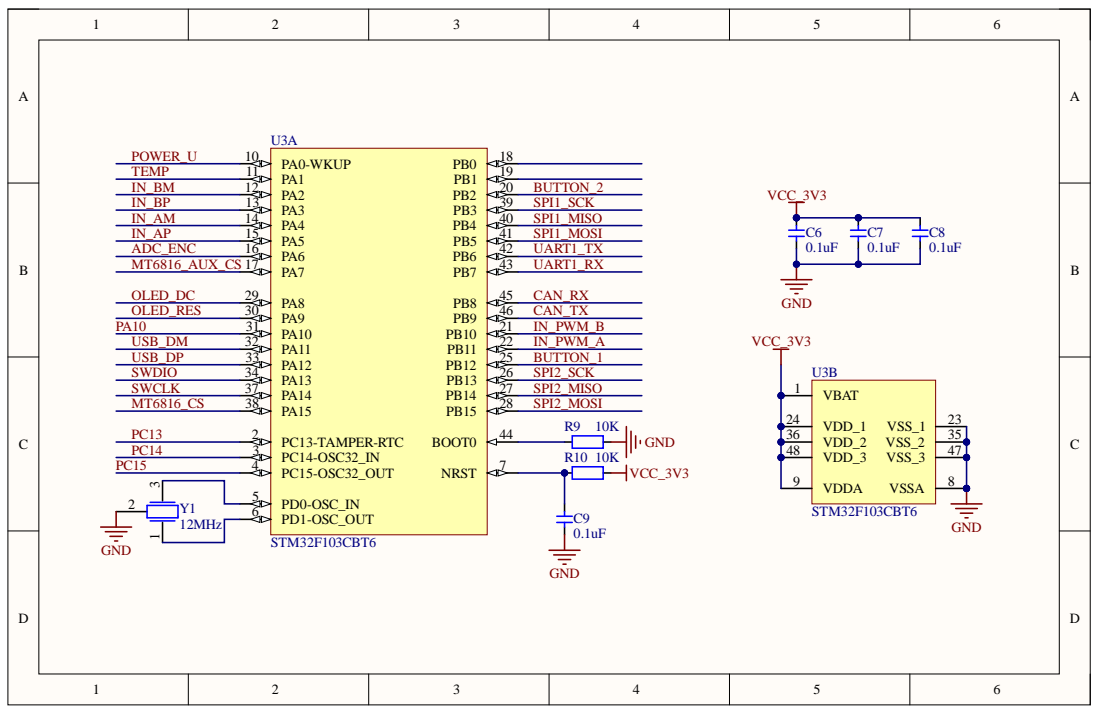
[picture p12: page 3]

PD0-OSC_IN 5

12MHz

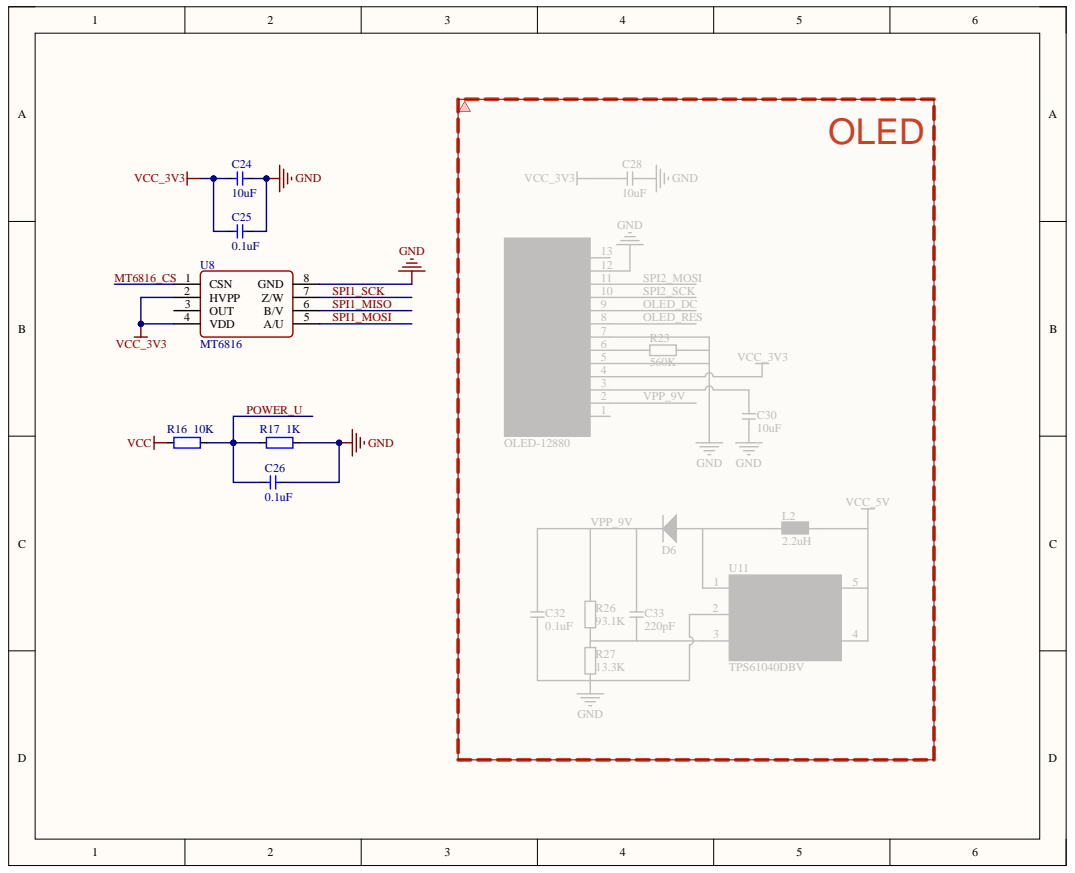
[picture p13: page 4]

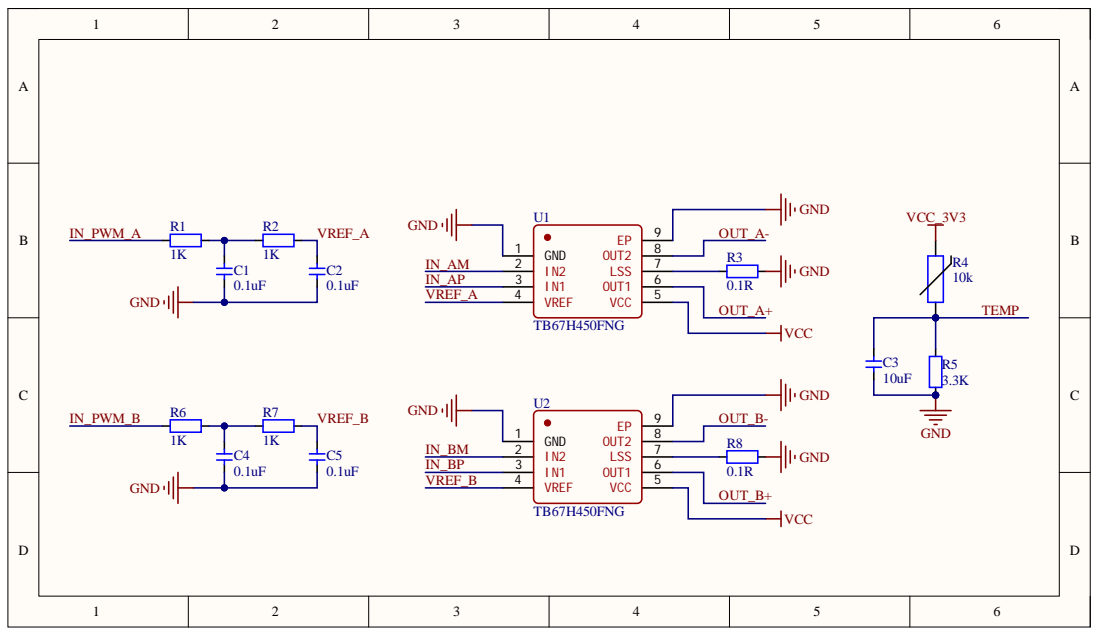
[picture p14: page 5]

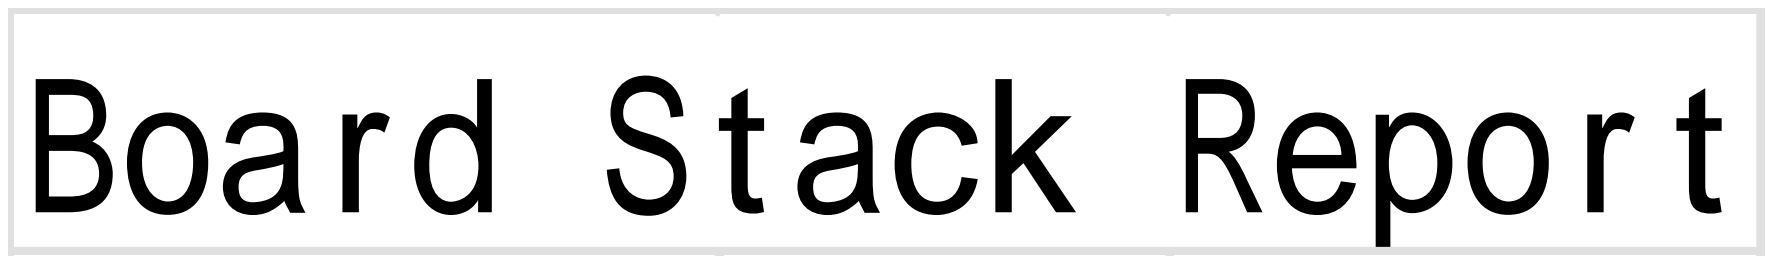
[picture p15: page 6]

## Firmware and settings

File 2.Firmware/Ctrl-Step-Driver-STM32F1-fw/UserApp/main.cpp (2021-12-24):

#include "common_inc.h"
#include "configurations.h"
#include "Platform/Utils/st_hardware.h"
#include <tim.h>


/* Component Definitions -----------------------------------------------------*/
BoardConfig_t boardConfig;
Motor motor;
TB67H450 tb67H450;
MT6816 mt6816;
EncoderCalibrator encoderCalibrator(&motor);
Button button1(1, 1000), button2(2, 3000);
void OnButton1Event(Button::Event _event);
void OnButton2Event(Button::Event _event);
Led statusLed;


/* Main Entry ----------------------------------------------------------------*/
void Main()
{
    uint64_t serialNum = GetSerialNumber();
    uint16_t defaultNodeID = 0;
    // Change below to fit your situation
    switch (serialNum)
    {
        case 431466563640: //J1
            defaultNodeID = 1;
            break;
        case 384624576568: //J2
            defaultNodeID = 2;
            break;
        case 384290670648: //J3
            defaultNodeID = 3;
            break;
        case 431531051064: //J4
            defaultNodeID = 4;
            break;
        case 431466760248: //J5
            defaultNodeID = 5;
            break;
        case 431484848184: //J6
            defaultNodeID = 6;
            break;
        default:
            break;
    }


    /*---------- Apply EEPROM Settings ----------*/
    // Setting priority is EEPROM > Motor.h
    EEPROM eeprom;
    eeprom.get(0, boardConfig);
    if (boardConfig.configStatus != CONFIG_OK) // use default settings
    {
        boardConfig = BoardConfig_t{
            .configStatus = CONFIG_OK,
            .canNodeId = defaultNodeID,
            .encoderHomeOffset = 0,
            .defaultMode = Motor::MODE_COMMAND_POSITION,
            .currentLimit = 1 * 1000,    // A
            .velocityLimit = 30 * motor.MOTOR_ONE_CIRCLE_SUBDIVIDE_STEPS, // r/s
            .velocityAcc = 100 * motor.MOTOR_ONE_CIRCLE_SUBDIVIDE_STEPS,   // r/s^2
            .calibrationCurrent=2000,
            .dce_kp = 200,
            .dce_kv = 80,
            .dce_ki = 300,
            .dce_kd = 250,
            .enableMotorOnBoot=false,
            .enableStallProtect=false
        };
        eeprom.put(0, boardConfig);
    }
    motor.config.motionParams.encoderHomeOffset = boardConfig.encoderHomeOffset;
    motor.config.motionParams.ratedCurrent = boardConfig.currentLimit;
    motor.config.motionParams.ratedVelocity = boardConfig.velocityLimit;
    motor.config.motionParams.ratedVelocityAcc = boardConfig.velocityAcc;
    motor.motionPlanner.velocityTracker.SetVelocityAcc(boardConfig.velocityAcc);
    motor.motionPlanner.positionTracker.SetVelocityAcc(boardConfig.velocityAcc);
    motor.config.motionParams.caliCurrent = boardConfig.calibrationCurrent;
    motor.config.ctrlParams.dce.kp = boardConfig.dce_kp;
    motor.config.ctrlParams.dce.kv = boardConfig.dce_kv;
    motor.config.ctrlParams.dce.ki = boardConfig.dce_ki;
    motor.config.ctrlParams.dce.kd = boardConfig.dce_kd;
    motor.config.ctrlParams.stallProtectSwitch = boardConfig.enableStallProtect;


    /*---------------- Init Motor ----------------*/
    motor.AttachDriver(&tb67H450);
    motor.AttachEncoder(&mt6816);
    motor.controller->Init();
    motor.driver->Init();
    motor.encoder->Init();


    /*------------- Init peripherals -------------*/
    button1.SetOnEventListener(OnButton1Event);
    button2.SetOnEventListener(OnButton2Event);


    /*------- Start Close-Loop Control Tick ------*/
    HAL_Delay(100);
    HAL_TIM_Base_Start_IT(&htim1);  // 100Hz
    HAL_TIM_Base_Start_IT(&htim4);  // 20kHz

    if (button1.IsPressed() && button2.IsPressed())
        encoderCalibrator.isTriggered = true;


    for (;;)
    {
        encoderCalibrator.TickMainLoop();


        if (boardConfig.configStatus == CONFIG_COMMIT)
        {
            boardConfig.configStatus = CONFIG_OK;
            eeprom.put(0, boardConfig);
        } else if (boardConfig.configStatus == CONFIG_RESTORE)
        {
            eeprom.put(0, boardConfig);
            HAL_NVIC_SystemReset();
        }
    }
}


/* Event Callbacks -----------------------------------------------------------*/
extern "C" void Tim1Callback100Hz()
{
    __HAL_TIM_CLEAR_IT(&htim1, TIM_IT_UPDATE);

    button1.Tick(10);
    button2.Tick(10);
    statusLed.Tick(10, motor.controller->state);
}


extern "C" void Tim4Callback20kHz()
{
    __HAL_TIM_CLEAR_IT(&htim4, TIM_IT_UPDATE);

    if (encoderCalibrator.isTriggered)
        encoderCalibrator.Tick20kHz();
    else
        motor.Tick20kHz();
}


void OnButton1Event(Button::Event _event)
{
    switch (_event)
    {
        case ButtonBase::UP:
            break;
        case ButtonBase::DOWN:
            break;
        case ButtonBase::LONG_PRESS:
            HAL_NVIC_SystemReset();
            break;
        case ButtonBase::CLICK:
            if (motor.controller->modeRunning != Motor::MODE_STOP)
            {
                boardConfig.defaultMode = motor.controller->modeRunning;
                motor.controller->requestMode = Motor::MODE_STOP;
            } else
            {
                motor.controller->requestMode = static_cast<Motor::Mode_t>(boardConfig.defaultMode);
            }
            break;
    }
}


void OnButton2Event(Button::Event _event)
{
    switch (_event)
    {
        case ButtonBase::UP:
            break;
        case ButtonBase::DOWN:
            break;
        case ButtonBase::LONG_PRESS:
            switch (motor.controller->modeRunning)
            {
                case Motor::MODE_COMMAND_CURRENT:
                case Motor::MODE_PWM_CURRENT:
                    motor.controller->SetCurrentSetPoint(0);
                    break;
                case Motor::MODE_COMMAND_VELOCITY:
                case Motor::MODE_PWM_VELOCITY:
                    motor.controller->SetVelocitySetPoint(0);
                    break;
                case Motor::MODE_COMMAND_POSITION:
                case Motor::MODE_PWM_POSITION:
                    motor.controller->SetPositionSetPoint(0);
                    break;
                case Motor::MODE_COMMAND_Trajectory:
                case Motor::MODE_STEP_DIR:
                case Motor::MODE_STOP:
                    break;
            }
            break;
        case ButtonBase::CLICK:
            motor.controller->ClearStallFlag();
            break;
    }
}

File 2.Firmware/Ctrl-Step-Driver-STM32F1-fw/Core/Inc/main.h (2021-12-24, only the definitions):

#define LED1_Pin GPIO_PIN_13
#define LED1_GPIO_Port GPIOC
#define LED2_Pin GPIO_PIN_14
#define LED2_GPIO_Port GPIOC
#define POWER_U_Pin GPIO_PIN_0
#define POWER_U_GPIO_Port GPIOA
#define DRV_TEMP_Pin GPIO_PIN_1
#define DRV_TEMP_GPIO_Port GPIOA
#define HW_ELEC_BM_Pin GPIO_PIN_2
#define HW_ELEC_BM_GPIO_Port GPIOA
#define HW_ELEC_BP_Pin GPIO_PIN_3
#define HW_ELEC_BP_GPIO_Port GPIOA
#define HW_ELEC_AM_Pin GPIO_PIN_4
#define HW_ELEC_AM_GPIO_Port GPIOA
#define HW_ELEC_AP_Pin GPIO_PIN_5
#define HW_ELEC_AP_GPIO_Port GPIOA
#define SIGNAL_COUNT_DIR_Pin GPIO_PIN_7
#define SIGNAL_COUNT_DIR_GPIO_Port GPIOA
#define SIGNAL_COUNT_DIR_EXTI_IRQn EXTI9_5_IRQn
#define SIGNAL_COUNT_EN_Pin GPIO_PIN_0
#define SIGNAL_COUNT_EN_GPIO_Port GPIOB
#define SIGNAL_ALERT_Pin GPIO_PIN_1
#define SIGNAL_ALERT_GPIO_Port GPIOB
#define BUTTON2_Pin GPIO_PIN_2
#define BUTTON2_GPIO_Port GPIOB
#define HW_ELEC_BPWM_Pin GPIO_PIN_10
#define HW_ELEC_BPWM_GPIO_Port GPIOB
#define HW_ELEC_APWM_Pin GPIO_PIN_11
#define HW_ELEC_APWM_GPIO_Port GPIOB
#define BUTTON1_Pin GPIO_PIN_12
#define BUTTON1_GPIO_Port GPIOB
#define SPI1_CS_Pin GPIO_PIN_15
#define SPI1_CS_GPIO_Port GPIOA

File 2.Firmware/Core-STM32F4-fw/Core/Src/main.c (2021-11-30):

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
/* Includes ------------------------------------------------------------------*/
#include "main.h"
#include "cmsis_os.h"
#include "adc.h"
#include "can.h"
#include "dma.h"
#include "i2c.h"
#include "spi.h"
#include "tim.h"
#include "usart.h"
#include "usb_device.h"
#include "gpio.h"


/* USER CODE BEGIN PV */
uint64_t serialNumber;
char serialNumberStr[13];
__attribute__((section(".ccmram"))) uint8_t ucHeap[configTOTAL_HEAP_SIZE];
/* USER CODE END PV */

void SystemClock_Config(void);
void MX_FREERTOS_Init(void);
/**
  * @brief  The application entry point.
  * @retval int
  */
int main(void)
{
  /* USER CODE BEGIN 1 */

    // This procedure of building a USB serial number should be identical
    // to the way the STM's built-in USB bootloader does it. This means
    // that the device will have the same serial number in normal and DFU mode.
    uint32_t uuid0 = *(uint32_t *) (UID_BASE + 0);
    uint32_t uuid1 = *(uint32_t *) (UID_BASE + 4);
    uint32_t uuid2 = *(uint32_t *) (UID_BASE + 8);
    uint32_t uuid_mixed_part = uuid0 + uuid2;
    serialNumber = ((uint64_t) uuid_mixed_part << 16) | (uint64_t) (uuid1 >> 16);

    uint64_t val = serialNumber;
    for (size_t i = 0; i < 12; ++i)
    {
        serialNumberStr[i] = "0123456789ABCDEF"[(val >> (48 - 4)) & 0xf];
        val <<= 4;
    }
    serialNumberStr[12] = 0;

  /* USER CODE END 1 */

  /* MCU Configuration--------------------------------------------------------*/

  /* Reset of all peripherals, Initializes the Flash interface and the Systick. */
  HAL_Init();

  /* USER CODE BEGIN Init */
    HAL_RCC_DeInit();

  /* USER CODE END Init */

  /* Configure the system clock */
  SystemClock_Config();

  /* Initialize all configured peripherals */
  MX_GPIO_Init();
  MX_DMA_Init();
  MX_I2C1_Init();
  MX_I2C2_Init();
  MX_CAN1_Init();
  MX_CAN2_Init();
  MX_USART1_UART_Init();
  MX_I2C3_Init();
  MX_SPI1_Init();
  MX_SPI3_Init();
  MX_UART4_Init();
  MX_ADC1_Init();
  MX_UART5_Init();
  MX_TIM2_Init();
  MX_TIM3_Init();
  /* Init scheduler */
  osKernelInitialize();  /* Call init function for freertos objects (in freertos.c) */
  MX_FREERTOS_Init();
  /* Start scheduler */
  osKernelStart();

  /* We should never get here as control is now taken by the scheduler */
  /* Infinite loop */
  /* USER CODE BEGIN WHILE */

    while (1)
    {
    /* USER CODE END WHILE */

    /* USER CODE BEGIN 3 */
    }
  /* USER CODE END 3 */
}

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
/* USER CODE BEGIN 4 */
void OnTimerCallback(TIM_TypeDef *timInstance);
/* USER CODE END 4 */

 /**
  * @brief  Period elapsed callback in non blocking mode
  * @note   This function is called  when TIM6 interrupt took place, inside
  * HAL_TIM_IRQHandler(). It makes a direct call to HAL_IncTick() to increment
  * a global variable "uwTick" used as application time base.
  * @param  htim : TIM handle
  * @retval None
  */
void HAL_TIM_PeriodElapsedCallback(TIM_HandleTypeDef *htim)
{
  if (htim->Instance == TIM6) {
    HAL_IncTick();
  }
  /* USER CODE BEGIN Callback 1 */
  else
  {
      OnTimerCallback(htim->Instance);
  }
  /* USER CODE END Callback 1 */
}

/**
  * @brief  This function is executed in case of error occurrence.
  * @retval None
  */
void Error_Handler(void)
{
  /* USER CODE BEGIN Error_Handler_Debug */
    /* User can add his own implementation to report the HAL error return state */
    __disable_irq();
    while (1)
    {
    }
  /* USER CODE END Error_Handler_Debug */
}

#ifdef  USE_FULL_ASSERT
/**
  * @brief  Reports the name of the source file and the source line number
  *         where the assert_param error has occurred.
  * @param  file: pointer to the source file name
  * @param  line: assert_param error line source number
  * @retval None
  */
void assert_failed(uint8_t *file, uint32_t line)
{
  /* USER CODE BEGIN 6 */
  /* User can add his own implementation to report the file name and line number,
     ex: printf("Wrong parameters value: file %s on line %d\r\n", file, line) */
  /* USER CODE END 6 */
}
#endif /* USE_FULL_ASSERT */

/************************ (C) COPYRIGHT STMicroelectronics *****END OF FILE****/

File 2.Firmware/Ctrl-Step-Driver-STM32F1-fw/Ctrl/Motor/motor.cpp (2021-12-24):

#include "configurations.h"
#include "motor.h"

#include <cmath>


void Motor::Tick20kHz()
{
    // 1.Encoder data Update
    encoder->UpdateAngle();

    // 2.Motor Control Update
    CloseLoopControlTick();
}


void Motor::AttachEncoder(EncoderBase* _encoder)
{
    encoder = _encoder;
}


void Motor::AttachDriver(DriverBase* _driver)
{
    driver = _driver;
}


void Motor::CloseLoopControlTick()
{
    /************************************ First Called ************************************/
    static bool isFirstCalled = true;
    if (isFirstCalled)
    {
        int32_t angle;
        if (config.motionParams.encoderHomeOffset < MOTOR_ONE_CIRCLE_SUBDIVIDE_STEPS / 2)
        {
            angle =
                encoder->angleData.rectifiedAngle >
                config.motionParams.encoderHomeOffset + MOTOR_ONE_CIRCLE_SUBDIVIDE_STEPS / 2 ?
                encoder->angleData.rectifiedAngle - MOTOR_ONE_CIRCLE_SUBDIVIDE_STEPS :
                encoder->angleData.rectifiedAngle;
        } else
        {
            angle =
                encoder->angleData.rectifiedAngle <
                config.motionParams.encoderHomeOffset - MOTOR_ONE_CIRCLE_SUBDIVIDE_STEPS / 2 ?
                encoder->angleData.rectifiedAngle + MOTOR_ONE_CIRCLE_SUBDIVIDE_STEPS :
                encoder->angleData.rectifiedAngle;
        }

        controller->realLapPosition = angle;
        controller->realLapPositionLast = angle;
        controller->realPosition = angle;
        controller->realPositionLast = angle;

        isFirstCalled = false;
        return;
    }

    /********************************* Update Data *********************************/
    int32_t deltaLapPosition;

    // Read Encoder data
    controller->realLapPositionLast = controller->realLapPosition;
    controller->realLapPosition = encoder->angleData.rectifiedAngle;

    // Lap-Position calculate
    deltaLapPosition = controller->realLapPosition - controller->realLapPositionLast;
    if (deltaLapPosition > MOTOR_ONE_CIRCLE_SUBDIVIDE_STEPS >> 1)
        deltaLapPosition -= MOTOR_ONE_CIRCLE_SUBDIVIDE_STEPS;
    else if (deltaLapPosition < -MOTOR_ONE_CIRCLE_SUBDIVIDE_STEPS >> 1)
        deltaLapPosition += MOTOR_ONE_CIRCLE_SUBDIVIDE_STEPS;

    // Naive-Position calculate
    controller->realPositionLast = controller->realPosition;
    controller->realPosition += deltaLapPosition;

    /********************************* Estimate Data *********************************/
    // Estimate Velocity
    controller->estVelocityIntegral += (
        (controller->realPosition - controller->realPositionLast) * motionPlanner.CONTROL_FREQUENCY
        + ((controller->estVelocity << 5) - controller->estVelocity)
    );
    controller->estVelocity = controller->estVelocityIntegral >> 5;
    controller->estVelocityIntegral -= (controller->estVelocity << 5);

    // Estimate Position
    controller->estLeadPosition = Controller::CompensateAdvancedAngle(controller->estVelocity);
    controller->estPosition = controller->realPosition + controller->estLeadPosition;

    // Estimate Error
    controller->estError = controller->softPosition - controller->estPosition;

    /************************************ Ctrl Loop ************************************/
    if (controller->isStalled ||
        controller->softDisable ||
        !encoder->IsCalibrated())
    {
        controller->ClearIntegral();    // clear integrals
        controller->focPosition = 0;    // clear outputs
        controller->focCurrent = 0;
        driver->Sleep();
    } else if (controller->softBrake)
    {
        controller->ClearIntegral();
        controller->focPosition = 0;
        controller->focCurrent = 0;
        driver->Brake();
    } else
    {
        switch (controller->modeRunning)
        {
            case MODE_STEP_DIR:
                controller->CalcDceToOutput(controller->softPosition, controller->softVelocity);
                break;
            case MODE_STOP:
                driver->Sleep();
                break;
            case MODE_COMMAND_Trajectory:
                controller->CalcDceToOutput(controller->softPosition, controller->softVelocity);
                break;
            case MODE_COMMAND_CURRENT:
                controller->CalcCurrentToOutput(controller->softCurrent);
                break;
            case MODE_COMMAND_VELOCITY:
                controller->CalcPidToOutput(controller->softVelocity);
                break;
            case MODE_COMMAND_POSITION:
                controller->CalcDceToOutput(controller->softPosition, controller->softVelocity);
                break;
            case MODE_PWM_CURRENT:
                controller->CalcCurrentToOutput(controller->softCurrent);
                break;
            case MODE_PWM_VELOCITY:
                controller->CalcPidToOutput(controller->softVelocity);
                break;
            case MODE_PWM_POSITION:
                controller->CalcDceToOutput(controller->softPosition, controller->softVelocity);
                break;
            default:
                break;
        }
    }

    /******************************* Mode Change Handle *******************************/
    if (controller->modeRunning != controller->requestMode)
    {
        controller->modeRunning = controller->requestMode;
        controller->softNewCurve = true;
    }

    /******************************* Update Hard-Goal *******************************/
    if (controller->goalVelocity > config.motionParams.ratedVelocity)
        controller->goalVelocity = config.motionParams.ratedVelocity;
    else if (controller->goalVelocity < -config.motionParams.ratedVelocity)
        controller->goalVelocity = -config.motionParams.ratedVelocity;
    if (controller->goalCurrent > config.motionParams.ratedCurrent)
        controller->goalCurrent = config.motionParams.ratedCurrent;
    else if (controller->goalCurrent < -config.motionParams.ratedCurrent)
        controller->goalCurrent = -config.motionParams.ratedCurrent;

    /******************************** Motion Plan *********************************/
    if ((controller->softDisable && !controller->goalDisable) ||
        (controller->softBrake && !controller->goalBrake))
    {
        controller->softNewCurve = true;
    }

    if (controller->softNewCurve)
    {
        controller->softNewCurve = false;
        controller->ClearIntegral();
        controller->ClearStallFlag();
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

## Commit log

2021-10-10 [Hw] Add hand module & LED ring PCBs.
    [HandModule.PrjPCB, LedRing.PcbDoc, LedRing.PrjPCB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]
2021-10-10 [Hw] Add controller PCB.
    [Controller.PcbDoc, Controller.PrjPCB, Main.SchDoc]
2021-10-10 [Hw] Add dongle PCB file.
    [Dangle.PcbDoc, Dangle.PrjPCB, Main.SchDoc]
2021-10-11 [Hw] Add REF PCB.
    [Main.SchDoc, REF-Base.PrjPCB, REF-Unit.PrjPCB]
2021-10-13 [Sw] Add DummyStudio.
    [serial_config.txt]
2021-10-27 [Fw] Add Dummy controller firmware.
    Add description of Firmware.
    [Controller.PcbDoc, Controller.PrjPCB, Dangle.PcbDoc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]
2021-11-04 [Hw] Add Step-Motor driver PCB.
    [Drive.SchDoc, Interface.SchDoc, MCU.SchDoc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]
2021-11-09 [Hw] Fix StepMotor-Drive-42 connector net missing problem.
    [Motor-42.PrjPCB]
2021-11-27 [Hw] Add MotorDriver-20.
    [Drive.SchDoc, Interface.SchDoc, MCU.SchDoc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]
2021-11-30 [Fw] Update Core-STM32 firmware.
    [stlink.cfg]
2021-12-24 [Fw] Add Ctrl-Step Driver firmware source-code & hex.
    [configurations.h, stlink.cfg]
2022-01-18 [Hw] Update Motor-42 hardware, add dual-encoder support.
    [Interface.SchDoc, MCU.SchDoc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]
2022-01-18 [Hw] Add Driver Motor-57 hardware design.
    [Drive.SchDoc, Interface.SchDoc, MCU.SchDoc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]
2022-01-18 [Hw] Add schematic PDF.
2022-02-09 [Sw] Add zadig driver.
    Update README.md
2022-03-01 [Model] Add case file.
2022-07-26 [3D] Add Ctrl Step heat sink.
    [Motor42-上盖.step, Motor42-下盖.step]

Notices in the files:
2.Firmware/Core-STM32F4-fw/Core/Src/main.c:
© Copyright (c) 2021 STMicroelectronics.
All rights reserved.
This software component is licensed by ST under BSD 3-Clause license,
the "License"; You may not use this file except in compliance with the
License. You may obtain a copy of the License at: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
